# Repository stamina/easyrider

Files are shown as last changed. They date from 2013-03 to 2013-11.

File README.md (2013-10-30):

EasyRider
=========

EasyRider is a motorcycle telemetrics project, developed specifically for my Honda C90 classic bike.

The software is written in C for the Atmel AVR ATmega1284p main microcontroller.

The PCB was created with CadSoft Eagle 6.x, you'll find the schematic and board layout (including all components) in the /eagle directory.
The file /doc/info.txt also contains the [BOM] and some project notes. (Partly in Dutch)

_UPDATE:_ EasyRider REV B (github repo: easyriderb) is a completely new, smaller and more advanced board (mostly SMD parts) which also contains a GPS and WiFi module
for easy tracking and communicating with a mobile phone app.

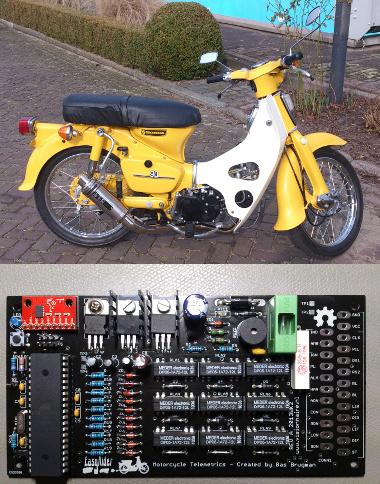
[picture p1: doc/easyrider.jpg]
Board and Bike


Functionality
-------------

EasyRider basically does the following things:

- Controls the lighting system: indicators, rear light, brake light, etc.
- Controls the claxon
- Contains a simple alarm system, based on an accelerometer
- Reads the motorcycle battery and gives a visual indication of the current voltage
- Contains a little buzzer for some funny startup sounds
- Contains a custom serial UART shell for communication with a terminal program or another microcontroller

Software
--------

The sofware is built around a simple *State Machine* pattern: when the driver is braking or toggling a switch, the software
is sending an event, which is handled by the correct event handler based on the current state (a bitmask of multiple substates).

The buzzer music was created with the **MIDICSV** MIDI to CSV conversion tool. The midi2byte.rb Ruby script converts the
plaintext CSV to a C header file containing an array of music notes.

The custom UART shell code is capable of registering commands and command handlers. E.g. typing "help" or "show state" in TeraTerm, Minicom, Putty
or any other serial terminal program. (configuration: 19200 baud/8N1)

*[BOM]: Bill Of Materials

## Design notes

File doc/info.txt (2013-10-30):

*info.txt* easyrider
" vim: filetype=help foldmethod=marker foldmarker=<<<,>>> modifiable noreadonly tw=0
" Author: Bas Brugman
" Website: www.visionnaire.nl

EasyRider REV A (Throughhole Edition) Telemetrics
-------------------------------------------------

Firmware 1.0 bug fixes:
----------------------

[X] BUG: Claxon mosfet switched aan bij veel toeren, voor zeer korte tijd -> oscillation?
      -> FIXED: Gemeten met scope: elke keer precies 15ms gate trigger, dus physical sense (drukknop claxon) maakt
         contact -> vergroten van 3x 5ms "debouncing" algoritme in code naar 6x
      -> duikt de 12V op gate naar beneden? waarom?
      -> Cap ervoor zetten?
      -> Grotere input cap bij 12V Regulator -> 1000uf, niet te hoge dimensie
      -> Transistor base resistor van 10K naar 2200 ohm?
      -> Cooler verwijderen: te veel capacitance?
      -> extra flyback diode (schottky) parallel aan mosfet? 
[X] BUG: The claxon sound continues when turning the alarm off by turning the ignition key on 
[X] TODO: Alarm mode: indicator blink slower -> every 4 timer1 ticks: 1 tick on 
[X] TODO: Alarm trigger time should be faster, 
[X] BUG: Ignition off: disable all lights/sounds
[X] BUG: Cockpit status light stays lit in alarm/alarmsettle mode ->  unwanted check_battery_read() calls
[X] BUG: Hardware related:  when claxon (2 amp) is pushed, all reed relays switch on: short blinks of lights
      -> snubber/flyback diode proberen
      -> Ground path van claxon terugvoeren via draad naar accu min-pole om groundloops te voorkomen
[X] BUG: Alarm trigger werkt niet lekker: claxon/blinkers sequence niet goed en transition from alarm_settle/alarm states foutief

REV A
-----

Firmware 1.1 features:
----------------------

- [ ] Bij debounce checks, is shifting << 5 wel nodig?
- [ ] Sound: Mountain King song erbij
- [ ] Change alarm claxon algorithme: count and resettle, ander algoritme -> 3de claxon sound kapt af, waarom?
- [ ] Extra timer gebruiken en flexibler/indepent maken van elkaar: losse blink timer
- [ ] Heartbeat LED uit na enige tijd
- [ ] Contact uit -> naar sleep mode -> meteen muziek uit 
- [ ] Contact uit -> alarm switch kan nog geactiveerd worden -> moet niet kunnen 
- [ ] Muziek mag nooit met indicatie beeps conflicteren 
- [ ] Splitsen hardware/software version strings -> beide in EEPROM
- [ ] "static"s nalopen
- [ ] backpedal code eruit halen
- [ ] in deep-sleep mode kan de mcu alleen via reset gestart worden -> FIXME

Firmware 1.0 features:
----------------------

- [X] Lighting System
- [X] Audio through Claxon and Buzzer
- [X] Battery status
- [X] Alarm, triggered by an accelerometer

- [X] PCB creation via Eagle CAD

- General functionality:
  [X] State Machine rules "exclusive"/"inclusive"
      [X] positive and negative substates parsing
      [X] sense reading moet uit te zetten zijn: enableSense/disableSense
      [X] event dispatching via psense reads, maar ook via dynamic senses (dyn_senses)
  [X] JTD uitzetten, zodat de poorten normaal gebruikt kunnen worden ->
       An IO control bit "JTD" is available. Unlike the fuses this bit can be
       set at run-time allowing you to disable the JTAG / OCD functionality in software
       during program execution.
  [X] Watchdog aanzetten, tegen vastlopers!
  [X] In production: OCD uitzetten ivm extra stroomverbruik

- Audio
  [X] Simple music via buzzer (Midi to CSV to .h binary conversion)

 [X] Claxon
  [X] Sound on Push button

 - Battery status
    [X] knipper status light cockpit:
      [X] normal operation -> continue branden
      [X] shutdown via switch -> uit
      [X] indien low battery -> slow knipper
      [X] indien high battery -> fast knipper

 - Alarm, triggered by an accelerometer
    [X] bij aanzetten -> 1x indicators aan voor x secs -> alarm settle time -> buzzer music
    [X] in active mode: cockpit indicator lamp knippert
    [X] Alarm triggered: alle lichten blinken, claxon repeat
    [X] Alarm triggered: na x secs -> reset -> accelerometer slaat nieuwe voltage waarden op

 - Light/Buzzer System
    [X] Indicators Left/Right
      [X] Buzzer mee laten piepen (software flag)
    [X] Rearlight
    [X] Brakelight
    [X] Pilotlight
    [X] Warning lights: 4x knipperbollen blinken en buzzer
    [X] Achteruitrij sensen met accelerometer -> "all indicators" en buzzer aan -> warning state

- Contact slot:
  Ignition uit: sense wire (SENSE_IGN) -> contact uit
    [X] naar ST_SLEEP mode
    [X] Na x secs naar mcu hardware sleep mode
      -> uitzetten van ADC, Watchdog en ports
      -> geen wakeup trigger, alleen een harde reset
  Ignition aan: sense wire (~SENSE_IGN) -> contact aan:
    [X] Alle lampen een paar seconden aan
    [X] startup sound / kleine muziekje
    [X] status wordt ST_NORMAL

- Shell Commands:
    [X] help -> show help menu / service menu
    [X] show
        [X] version
        [X] state (all substates / physical and dynamic senses)
        [X] volt (accu voltage / 3-axis voltages accelerometer)
        [X] conf (EEPROM struct, toon alle tSettings tegelijk):
    [X] set 
        [X] dynamic senses
        [X] conf (settings in EEPROM struct)
    [X] reset (software reset mcu via watchdog)

Statistics
----------

(2.9Ah Gel battery)

Power EasyRider Board REV A:
  Normal mode:     54mA
  Sleep mode:      44mA (pcb led brandt nog!)
  Alarm mode:      80mA (indicator relay on/off)
  Deep Sleep mode: 10mA (mcu Power Down) -> accu leeg na 12 dagen

BOM "EasyRider" REV A
---------------------

[X] 1x Atmel ATMEGA1284p 40 pins DIP
[X] 9x Meder Reed relays DIP05-1A72-12L 
[X] 10x 1N4007 diode
[X] 1x 1N5400 diode
[X] 11x 5.6V zener diode (10 senses, 1 voltage divider)
[X] 1x 100k resistor 1% 
[X] 1x 18k resistor 1% 
[X] 4x 10k resistor 5%  (pullups reset mcu and slp accelerometer en trans./mosfet gate)
[X] 11x 220 resistor 5% (10 senses, 1 heartbeat LED)
[X] 1x 330 resistor (reset btn current limiter)
[X] 1x 10 ohm 5 watt resistor
[X] 1x 6 amp fuse holder voor 5x20
[X] 1x 1A PTC 3,2 x 1,5 mm, hoog 1,05 mm -> van littelfuse "M" marking 15V!
[X] 1x 25V Varistor JVR05N390K (5mm pitch)
[X] 1x 470uf cap electrolytic for filtering 
[X] 1x 47uf low ESR cap electrolytic for filtering 
[X] 1x 10uf output filter cap for LF33CV
[X] 2x 100nf cap electrolytic for filtering
[X] 3x 100nf cap ceramic for bypassing
[X] 2x 22pf cap ceramic for crystal
[X] 1x 20mhz crystal
[X] 1x LM2940 regulator (TO-220)
[X] 1x LF33CV regulator (TO-220)
[X] 1x P-Channel MOSFET IRF4905PBF 
[X] 1x NPN 2N3904 transistor
[X] 1x reset button 4 pins 
[X] 1x buzzer (4.1khz 83db met sticker bovenop PK12N40PETQ)
[X] 1x 3mm blue status led 
[X] 1x shrouded ISP 6 pin (2x3) header (zie dangerousprototypes.com lib)
[X] 1x 2 pin header UART 
[X] 1x MMA7361 Freescale Accelerometer breakout pins 
[X] 1x 24 pin main wire connector

Extra: (external or added later on)
[X] 1x flyback diode parallel across claxon: SB540E SCHOTTKY 40V 5A
[X] 1x 1000uf cap electrolytic for filtering 

Schematic/Board
---------------

[X] ULP runnen voor re-ordering designators
[X] +/- 10 via's plaatsen voor koppelen GND planes 
[X] 4x drill hole 4mm (3mm x/y spacing zijkanten board)
[X] 2x drill hole 3mm voor accelerometer board stabiliteitspunten
[X] 4x Test Point TP (12v, 5V, 3.3v, GND) uit standard "testpad" library
[X] Import BMP logo met import-bmp.ulp, settings: Scaled, Mil, 0.3 Scale, Layer 21

Eagle settings:
--------------

- 1 oz copper thickness (35µm)
- diameter drills voor bevestiging +/- 3.5mm
- diameter voor via's = +/- 27 mil, voor 20 mil traces: 32 mil via's, let op dat outer-diameter niet te smal wordt:
    aanpassen restring -> iets groter zetten
- trace thickness:
    10 mil (1 amp) standaard SMD signal tracks
    16 mil (15-20 mil) for through-hole pads
    20 mil 3.3v/5v/12v seperate tracks/gnd tracks (3 amp)
    70 mil (6 amp) incoming 12v/GND track
- spacing between traces: minimum 10 mil 
- Isolation between GND polygons and other components/tracks: 15 mil
- Oval TH: 0.0314 inch (0.8 mm) diameter holes -> pad widths: 1.3-1.5 mm
- Oval TH: for 1mm2 draad (EasyRider connector): diameter holes: 1.9mm -> 0.074 inch
- Round TH: voor 1A diodes etc: 0.040 inch (1.1 mm) diameter holes
- Round TH: voor dikke 3A diodes etc: 0.059 inch (1.498 mm) diameter holes
- Round TH: voor standard diodes/resistors: 0.032 inch (0.81 mm) diameter holes
- Length/pitch for standard diodes/resistors: 0.4 inch (10.16 mm) of 0.5 inch (12.7 mm)
- Length/pitch for dikke high watt resistors: 1.15 inch (29.21 mm)
- text: always as vectors: 50 mil/0.05 inch size, 16% ratio == 8mil width, line distance 50%: (size*ratio/100 == width of text lines) 

Eagle layers:

- tNames: voor >NAME teksten
- tValues: voor >VALUE teksten
- tPlace: silkscreen lijnen/tekst/outlines -> (8 mil/0.008 inch width, gebruik een 0.025 inch afstandsgrid van pads/tracks: no overlapping!)
- tDocu: outlines van alle packages (alleen ter controle voor spacing en printouts: past het allemaal naast elkaar) -> geef een gele kleur (5 mil width)

EuroCircuits.com export settings:
---------------------------------

Gewoon de .brd uploaden, of:

CAM processor: gerb274x.cam

4 layers selecteren: Component side (.CMP)       = 1 Top layer / 17 Pads layer / 18 Vias layer / 20 Dimension layer
4 layers selecteren: Solder side (.SOL)          = 16 Bot layer / 17 Pads layer / 18 Vias layer / 20 Dimension layer
3 layers selecteren: Silk screen CMP (.PLC) 	   = 20 Dimension layer / 21 tPlace layer / 25 tNames layer
2 layers selecteren: Solder stop mask CMP (.STC) = 20 Dimension layer / 29 tStop layer
2 layers selecteren: Solder stop mask SOL (.STS) = 20 Dimension layer / 30 bStop layer

CAM processor: excellon.cam

2 layers selecteren: Excellon drill (.DRD)       = 44 Drills layer / 45 Holes layer

NOTE: Cream (solderpaste) en milling/measures layers niet nodig.
      Let op dat alle .extensies uniek zijn!

You then click process job and the Excellon file will be generated.
You now simply combine all these files into a single zip file and upload it via the Eurocircuits website.

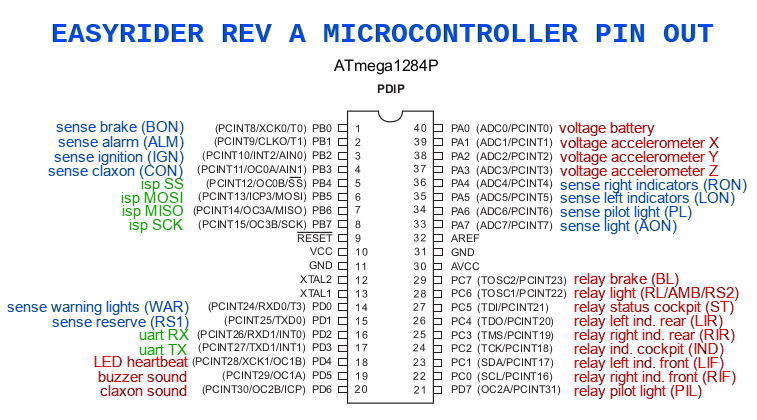
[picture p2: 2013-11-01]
doc/easyrider_reva_mcu_pinout.png

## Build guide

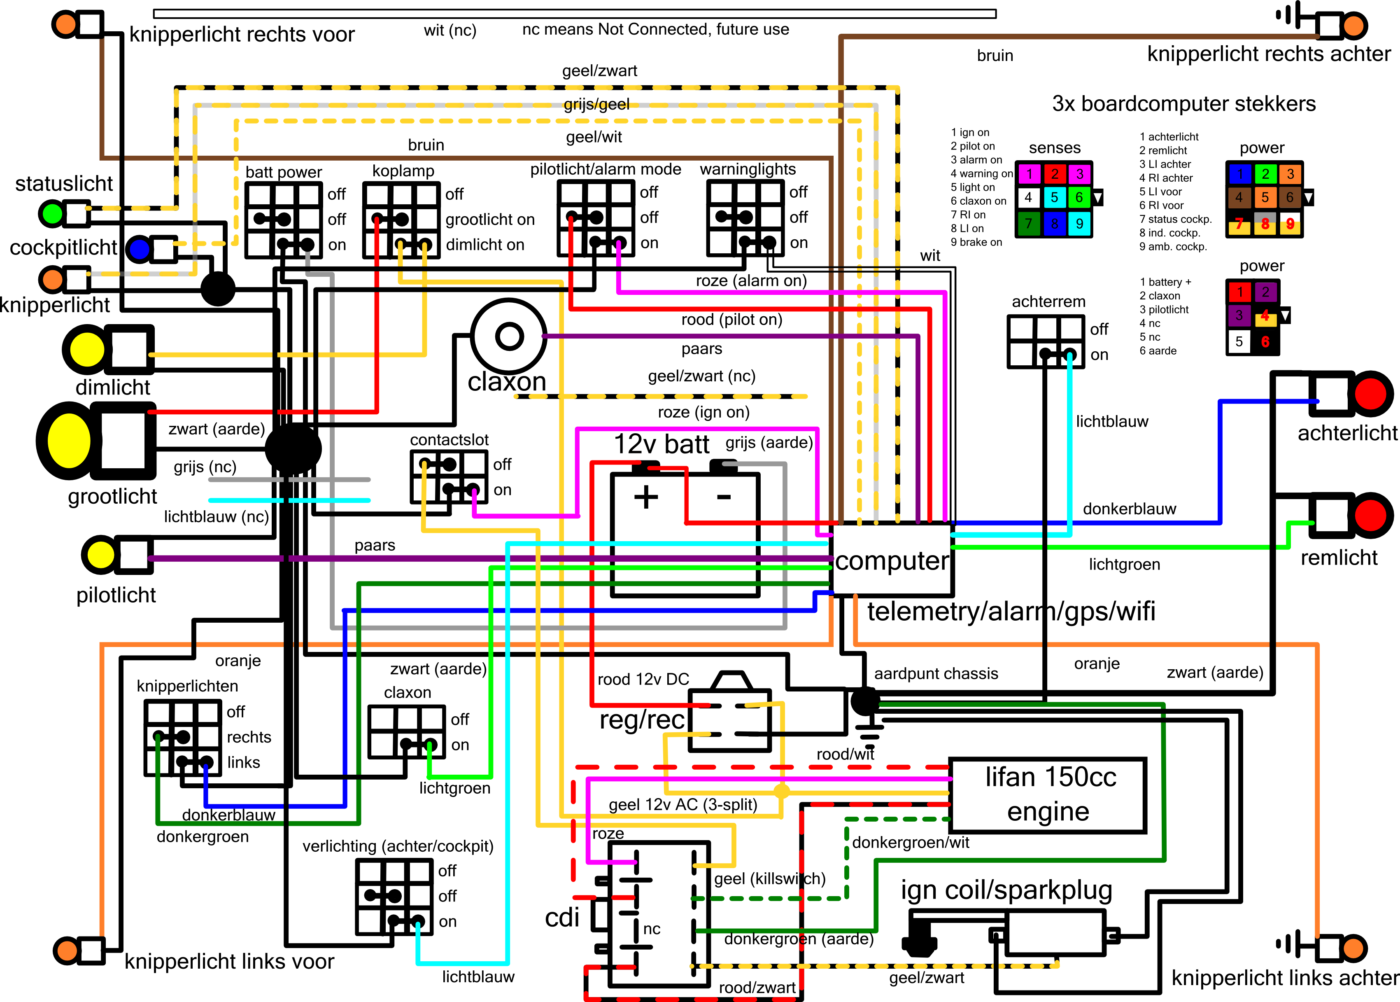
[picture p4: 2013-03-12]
doc/hondac90_lifan150_wiring.png

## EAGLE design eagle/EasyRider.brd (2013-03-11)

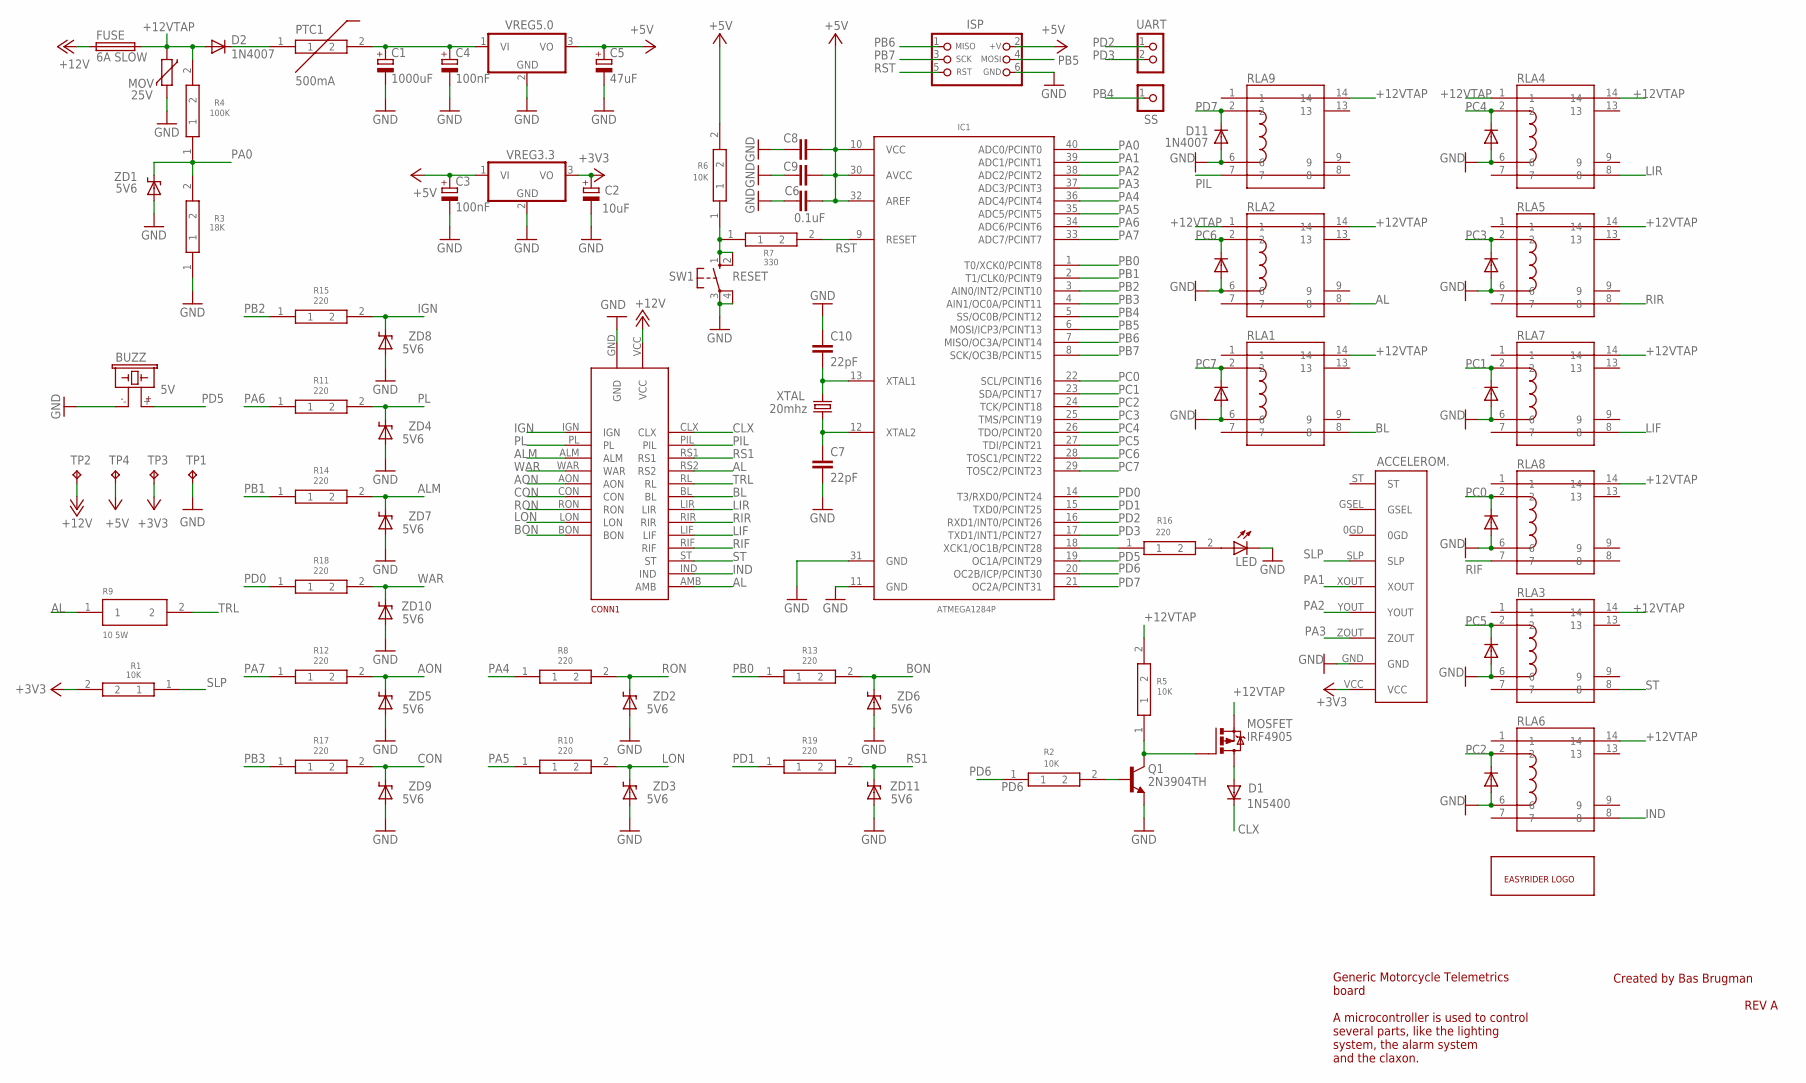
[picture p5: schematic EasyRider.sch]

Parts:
ACCELEROM.: MMA7361FREESCALE; BREAKOUT
BUZZ: 5V; 0.3PITCH
C1: 1000uF; E5-10,5
C2: 10uF; E2,5-4R
C3, C4: 100nF; E2,5-4R
C5: 47uF; E2,5-7
C6, C8, C9: 0.1uF; C025-024X044
C7, C10: 22pF; C025-024X044
CONN1: EASYRIDER_CONNDIP; SIL
D1: 1N5400; DO201-15
D2, D11: 1N4007; DIP_1N4007
D3, D4, D5, D6, D7, D8, D9, D10: 1N4007DIP; DIP_1N4007
FUSE: 6A SLOW; SH22,5A
IC1: ATMEGA1284P; DIL40
ISP: CON_HEADER_PRG_AVR_ICSP-PTH; HEADER_PRG_2X03
LED: LEDDIP; LED3MM
MOSFET: IRF4905; TO220
MOV: 25V; R-5
PTC1: 500mA; PTC
Q1: 2N3904TH; TO92
R1, R2, R5, R6: 10K; RESISTOR
R3: 18K; RESISTOR
R4: 100K; RESISTOR
R7: 330; RESISTOR
R8, R10, R11, R12, R13, R14, R15, R16, R17, R18, R19: 220; RESISTOR
R9: 10 5W; RESISTOR
RLA1, RLA2, RLA3, RLA4, RLA5, RLA6, RLA7, RLA8, RLA9: MEDER_REED_DIP05-1A72-12LDIP; DIP05-1A72-12L
SS: CON_HEADER_1X01-PTH; M1X1
SW1: RESET; DIP45MM_56MM_PITCH
TP1, TP2, TP3, TP4: TPTP20SQ; TP20SQ
U$1: EASYRIDER_LOGO
UART: CON_HEADER_1X02-PTH; M1X2
VREG3.3, VREG5.0: VREG_IGODIP; TO220
XTAL: 20mhz; HC49/S
ZD1, ZD2, ZD3, ZD4, ZD5, ZD6, ZD7, ZD8, ZD9, ZD10, ZD11: 5V6; DIODE_ZENER_56

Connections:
+3V3: ACCELEROM..VCC, C2.+, R1.2, TP3.TP, VREG3.3.3 (VO)
+5V: C3.+, C5.+, C6.2, C8.2, C9.2, IC1.10 (VCC), IC1.30 (AVCC), IC1.32 (AREF), ISP.2 (+V), R6.2, TP4.TP, VREG3.3.1 (VI), VREG5.0.3 (VO)
+12V: CONN1.VCC, FUSE.1, TP2.TP
+12VTAP: D2.A, FUSE.2, MOSFET.S, MOV.1, R4.2, R5.2, RLA1.14, RLA2.1, RLA2.14, RLA3.14, RLA4.1, RLA4.14, RLA5.14, RLA6.14, RLA7.14, RLA8.14, RLA9.14
AL: CONN1.AMB, CONN1.RS2, R9.1, RLA2.8
ALM: CONN1.ALM, R14.2, ZD7.C
AON: CONN1.AON, R12.2, ZD5.C
BL: CONN1.BL, RLA1.8
BON: CONN1.BON, R13.2, ZD6.C
CLX: CONN1.CLX, D1.C
CON: CONN1.CON, R17.2, ZD9.C
GND: ACCELEROM..GND, BUZZ.- (1), C1.-, C2.-, C3.-, C4.-, C5.-, C6.1, C7.2, C8.1, C9.1, C10.1, CONN1.GND, D3.A, D4.A, D5.A, D6.A, D7.A, D8.A, D9.A, D10.A, D11.A, IC1.11 (GND), IC1.31 (GND), ISP.6 (GND), LED.K (C), MOV.2, Q1.3 (E), R3.1, RLA1.6, RLA2.6, RLA3.6, RLA4.6, RLA5.6, RLA6.6, RLA7.6, RLA8.6, RLA9.6, SW1.3, SW1.4, TP1.TP, VREG3.3.2 (GND), VREG5.0.2 (GND), ZD1.A, ZD2.A, ZD3.A, ZD4.A, ZD5.A, ZD6.A, ZD7.A, ZD8.A, ZD9.A, ZD10.A, ZD11.A
IGN: CONN1.IGN, R15.2, ZD8.C
IND: CONN1.IND, RLA6.8
LIF: CONN1.LIF, RLA7.8
LIR: CONN1.LIR, RLA4.8
LON: CONN1.LON, R10.2, ZD3.C
unnamed: C7.1, IC1.12 (XTAL2), XTAL.1
unnamed: C10.2, IC1.13 (XTAL1), XTAL.2
unnamed: R6.1, R7.1, SW1.1, SW1.2
unnamed: IC1.18 (XCK1/OC1B/PCINT28), R16.1
unnamed: MOSFET.G, Q1.1 (C), R5.1
unnamed: D1.A, MOSFET.D
unnamed: LED.A, R16.2
unnamed: C1.+, C4.+, PTC1.2, VREG5.0.1 (VI)
unnamed: D2.C, PTC1.1
unnamed: Q1.2 (B), R2.2
PA0: IC1.40 (ADC0/PCINT0), R3.2, R4.1, ZD1.C
PA1: ACCELEROM..XOUT, IC1.39 (ADC1/PCINT1)
PA2: ACCELEROM..YOUT, IC1.38 (ADC2/PCINT2)
PA3: ACCELEROM..ZOUT, IC1.37 (ADC3/PCINT3)
PA4: IC1.36 (ADC4/PCINT4), R8.1
PA5: IC1.35 (ADC5/PCINT5), R10.1
PA6: IC1.34 (ADC6/PCINT6), R11.1
PA7: IC1.33 (ADC7/PCINT7), R12.1
PB0: IC1.1 (T0/XCK0/PCINT8), R13.1
PB1: IC1.2 (T1/CLK0/PCINT9), R14.1
PB2: IC1.3 (AIN0/INT2/PCINT10), R15.1
PB3: IC1.4 (AIN1/OC0A/PCINT11), R17.1
PB4: IC1.5 (SS/OC0B/PCINT12), SS.1
PB5: IC1.6 (MOSI/ICP3/PCINT13), ISP.4 (MOSI)
PB6: IC1.7 (MISO/OC3A/PCINT14), ISP.1 (MISO)
PB7: IC1.8 (SCK/OC3B/PCINT15), ISP.3 (SCK)
PC0: D10.C, IC1.22 (SCL/PCINT16), RLA8.2
PC1: D9.C, IC1.23 (SDA/PCINT17), RLA7.2
PC2: D8.C, IC1.24 (TCK/PCINT18), RLA6.2
PC3: D7.C, IC1.25 (TMS/PCINT19), RLA5.2
PC4: D6.C, IC1.26 (TDO/PCINT20), RLA4.2
PC5: D5.C, IC1.27 (TDI/PCINT21), RLA3.2
PC6: D4.C, IC1.28 (TOSC1/PCINT22), RLA2.2
PC7: D3.C, IC1.29 (TOSC2/PCINT23), RLA1.2
PD0: IC1.14 (T3/RXD0/PCINT24), R18.1
PD1: IC1.15 (TXD0/PCINT25), R19.1
PD2: IC1.16 (RXD1/INT0/PCINT26), UART.1
PD3: IC1.17 (TXD1/INT1/PCINT27), UART.2
PD5: BUZZ.+ (2), IC1.19 (OC1A/PCINT29)
PD6: IC1.20 (OC2B/ICP/PCINT30), R2.1
PD7: D11.C, IC1.21 (OC2A/PCINT31), RLA9.2
PIL: CONN1.PIL, RLA9.7
PL: CONN1.PL, R11.2, ZD4.C
RIF: CONN1.RIF, RLA8.7
RIR: CONN1.RIR, RLA5.8
RON: CONN1.RON, R8.2, ZD2.C
RS1: CONN1.RS1, R19.2, ZD11.C
RST: IC1.9 (RESET), ISP.5 (RST), R7.2
SLP: ACCELEROM..SLP, R1.1
ST: CONN1.ST, RLA3.8
TRL: CONN1.RL, R9.2
WAR: CONN1.WAR, R18.2, ZD10.C

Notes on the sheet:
Created by Bas Brugman
REV A
Generic Motorcycle Telemetrics board A microcontroller is used to control several parts, like the lighting system, the alarm system and the claxon.

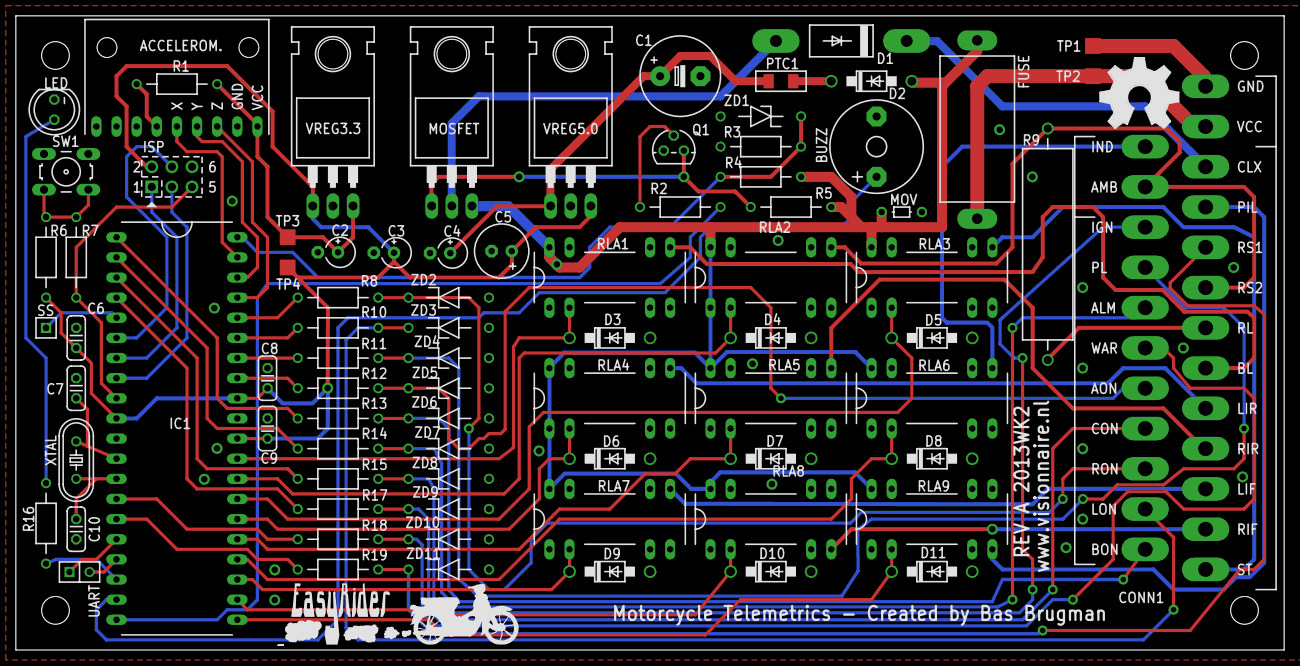
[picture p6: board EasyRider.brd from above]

Board: 2 copper layers, 160.0 x 80.0 mm, 83 parts (0 on the bottom side), 69 nets.

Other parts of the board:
U$2: OSHW_FILLX350_NOTEXT

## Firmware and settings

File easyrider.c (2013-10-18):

/*
 *
 *  Copyright (C) 2013 Bas Brugman
 *  http://www.visionnaire.nl
 *
 *  Licensed under the Apache License, Version 2.0 (the "License");
 *  you may not use this file except in compliance with the License.
 *  You may obtain a copy of the License at
 *
 *    http://www.apache.org/licenses/LICENSE-2.0
 *
 *  Unless required by applicable law or agreed to in writing, software
 *  distributed under the License is distributed on an "AS IS" BASIS,
 *  WITHOUT WARRANTIES OR CONDITIONS OF ANY KIND, either express or implied.
 *  See the License for the specific language governing permissions and
 *  limitations under the License.
 *
 */
#include <avr/io.h>
#include <avr/interrupt.h>
#include <avr/pgmspace.h>
#include <avr/eeprom.h>
#include <avr/wdt.h>
#include <avr/sleep.h>
#include <avr/power.h>
#include <stdlib.h>
#include <stdint.h>
#include <string.h>

#include "command.h"
#include "usart.h"
#include "command_usart.h"
#include "command_handlers.h"
#include "easyrider.h"

#include "sound/alarm.h"
#include "sound/frogger.h"
#include "sound/furelise.h"
#include "sound/larry.h"
#include "sound/pipi.h"
#include "sound/popcorn.h"

// state transition struct array: handler assigment for state/event combo's
tTransition g_trans[] = {
  {check_claxon_on, EV_CLAXON_ON, process_claxon_on},
  {check_claxon_off, EV_CLAXON_OFF, process_claxon_off},
  {check_ri_on, EV_RI_ON, process_ri_on},
  {check_ri_off, EV_RI_OFF, process_ri_off},
  {check_li_on, EV_LI_ON, process_li_on},
  {check_li_off, EV_LI_OFF, process_li_off},
  {check_ign_on, EV_IGN_ON, process_ign_on},
  {check_ign_off, EV_IGN_OFF, process_ign_off},
  {check_alarm_on, EV_ALARM_ON, process_alarm_on},
  {check_alarm_off, EV_ALARM_OFF, process_alarm_off},
  {check_brake_on, EV_BRAKE_ON, process_brake_on},
  {check_brake_off, EV_BRAKE_OFF, process_brake_off},
  {check_pilot_on, EV_PILOT_ON, process_pilot_on},
  {check_pilot_off, EV_PILOT_OFF, process_pilot_off},
  {check_light_on, EV_LIGHT_ON, process_light_on},
  {check_light_off, EV_LIGHT_OFF, process_light_off},
  {check_battery_read, EV_READ_BATT, process_battery},
  {check_warning_on, EV_WARNING_ON, process_warning_on},
  {check_warning_off, EV_WARNING_OFF, process_warning_off},
  {check_backpedal_on, EV_BACKPEDAL, process_backpedal}
};

static uint16_t get_substate(uint16_t st) {
  return (g_state & st);
}

static void set_substate(uint16_t st) {
  g_state |= st;
}

static void remove_substate(uint16_t st) {
  g_state &= ~st;
}

// Gets called from the main loop, reads all senses and puts them in the event queue.
// The complete queue is handled (emptied) in each main loop iteration in a FIFO way, so better
// put the higher priority events at the top, i.e. claxon sound is more important then indicator light.
static void dispatch_events() {
  check_brake();
  check_claxon();
  check_ri();
  check_li();
  check_light();
  check_pilot();
  check_ign();
  check_settle();
  check_sound();
  check_alarm();
  check_alarm_settle();
  check_alarm_trigger();
  check_battery();
  check_warning();
  check_sleep();
  if (g_settings.backpedal) {
    check_backpedal();
  }
}

uint8_t check_battery_read() {
  return ((g_state & ~(ST_ALARM | ST_ALARM_SETTLE | ST_SETTLE | ST_SLEEP)) == g_state);
}

uint8_t check_ri_on() {
  return (((g_state & (ST_NORMAL | ST_RI | ST_CLAXON | ST_BRAKE | ST_LIGHT | ST_PILOT)) == g_state) &&
        ((g_state & ~(ST_LI | ST_ALARM | ST_ALARM_SETTLE | ST_SETTLE | ST_WARNING | ST_SLEEP)) == g_state));
}

uint8_t check_li_on() {
  return (((g_state & (ST_NORMAL | ST_LI | ST_CLAXON | ST_BRAKE | ST_LIGHT | ST_PILOT)) == g_state) &&
        ((g_state & ~(ST_RI | ST_ALARM | ST_ALARM_SETTLE | ST_SETTLE | ST_WARNING | ST_SLEEP)) == g_state));
}

uint8_t check_brake_on() {
  return (((g_state & (ST_NORMAL | ST_RI | ST_LI | ST_CLAXON | ST_LIGHT | ST_PILOT | ST_WARNING)) == g_state) &&
        ((g_state & ~(ST_BRAKE | ST_ALARM | ST_ALARM_SETTLE | ST_SETTLE | ST_SLEEP)) == g_state));
}

uint8_t check_warning_on() {
  // warning blinks override RI/LI
  return (((g_state & (ST_NORMAL | ST_WARNING | ST_RI | ST_LI | ST_CLAXON | ST_LIGHT | ST_PILOT | ST_BRAKE )) == g_state) &&
        ((g_state & ~(ST_ALARM | ST_ALARM_SETTLE | ST_SETTLE | ST_SLEEP)) == g_state));
}

uint8_t check_pilot_on() {
  return (((g_state & (ST_NORMAL | ST_RI | ST_LI | ST_CLAXON | ST_LIGHT | ST_BRAKE | ST_WARNING)) == g_state) &&
        ((g_state & ~(ST_PILOT | ST_ALARM | ST_ALARM_SETTLE | ST_SETTLE | ST_SLEEP)) == g_state));
}

uint8_t check_light_on() {
  return (((g_state & (ST_NORMAL | ST_RI | ST_LI | ST_CLAXON | ST_PILOT | ST_BRAKE | ST_WARNING)) == g_state) &&
        ((g_state & ~(ST_LIGHT | ST_ALARM | ST_ALARM_SETTLE | ST_SETTLE | ST_SLEEP)) == g_state));
}

uint8_t check_backpedal_on() {
  return (((g_state & (ST_NORMAL | ST_LIGHT | ST_CLAXON | ST_PILOT | ST_BRAKE )) == g_state) &&
        ((g_state & ~(ST_WARNING | ST_RI | ST_LI | ST_ALARM | ST_ALARM_SETTLE | ST_SETTLE | ST_SLEEP)) == g_state));
}

uint8_t check_claxon_on() {
  return (((g_state & (ST_NORMAL | ST_RI | ST_LI | ST_BRAKE | ST_LIGHT | ST_PILOT | ST_WARNING)) == g_state) &&
        ((g_state & ~(ST_CLAXON | ST_ALARM | ST_ALARM_SETTLE | ST_SETTLE | ST_SLEEP)) == g_state));
}

uint8_t check_ign_on() {
  return ((g_state & (ST_SLEEP | ST_ALARM_SETTLE | ST_ALARM)) == g_state);
}

uint8_t check_alarm_on() {
  //BUG: change this..
  return ((g_state & ST_SLEEP) == g_state);
}

uint8_t check_ri_off() {
 return ((ST_RI & g_state) == ST_RI);
}

uint8_t check_li_off() {
 return ((ST_LI & g_state) == ST_LI);
}

uint8_t check_claxon_off() {
 return ((ST_CLAXON & g_state) == ST_CLAXON);
}

uint8_t check_pilot_off() {
 return ((ST_PILOT & g_state) == ST_PILOT);
}

uint8_t check_brake_off() {
 return ((ST_BRAKE & g_state) == ST_BRAKE);
}

uint8_t check_warning_off() {
 return ((ST_WARNING & g_state) == ST_WARNING);
}

uint8_t check_light_off() {
 return ((ST_LIGHT & g_state) == ST_LIGHT);
}

uint8_t check_ign_off() {
  return ((g_state & ~(ST_SLEEP | ST_ALARM | ST_ALARM_SETTLE)) == g_state);
}

uint8_t check_alarm_off() {
  // alarm can't be switched off in alarm state, only explicitly in alarm_settle mode
  // or automatically when ignition is switched on
  return ((g_state & (ST_ALARM_SETTLE)) == g_state);
}

void check_ri() {
  // pin senses
  if ((g_senses & FLAG_SENSE_LIGHT_RI) == FLAG_SENSE_LIGHT_RI) {
    if (~STATUS_C90_SENSE_LIGHT_RI) { // low, RI on
      set_event(EV_RI_ON);
    }
    if (STATUS_C90_SENSE_LIGHT_RI) { // RI off
      set_event(EV_RI_OFF);
    }
  }
  // dynamic senses
  if ((g_dyn_senses & FLAG_SENSE_LIGHT_RI) == FLAG_SENSE_LIGHT_RI) {
    if ((g_dyn_senses_status & FLAG_SENSE_LIGHT_RI) == FLAG_SENSE_LIGHT_RI) { // high, RI off
      set_event(EV_RI_OFF);
    } else {
      set_event(EV_RI_ON); // RI on
    }
  }
}

void check_li() {
  // pin senses
  if ((g_senses & FLAG_SENSE_LIGHT_LI) == FLAG_SENSE_LIGHT_LI) {
    if (~STATUS_C90_SENSE_LIGHT_LI) { // low, LI on
      set_event(EV_LI_ON);
    }
    if (STATUS_C90_SENSE_LIGHT_LI) { // LI off
      set_event(EV_LI_OFF);
    }
  }
  // dynamic senses
  if ((g_dyn_senses & FLAG_SENSE_LIGHT_LI) == FLAG_SENSE_LIGHT_LI) {
    if ((g_dyn_senses_status & FLAG_SENSE_LIGHT_LI) == FLAG_SENSE_LIGHT_LI) { // high, LI off
      set_event(EV_LI_OFF);
    } else {
      set_event(EV_LI_ON); // LI on
    }
  }
}

void check_claxon() {
  // pin senses
  if ((g_senses & FLAG_SENSE_CLAXON) == FLAG_SENSE_CLAXON) {
    if (~STATUS_C90_SENSE_CLAXON) {
      set_event(EV_CLAXON_ON);
    }
    if (STATUS_C90_SENSE_CLAXON) {
      set_event(EV_CLAXON_OFF);
    }
  }
  // dynamic senses
  if ((g_dyn_senses & FLAG_SENSE_CLAXON) == FLAG_SENSE_CLAXON) {
    if ((g_dyn_senses_status & FLAG_SENSE_CLAXON) == FLAG_SENSE_CLAXON) {
      set_event(EV_CLAXON_OFF);
    } else {
      set_event(EV_CLAXON_ON);
    }
  }
}

void check_pilot() {
  // pin senses
  if ((g_senses & FLAG_SENSE_PILOT) == FLAG_SENSE_PILOT) {
    if (~STATUS_C90_SENSE_PILOT) {
      set_event(EV_PILOT_ON);
    }
    if (STATUS_C90_SENSE_PILOT) {
      set_event(EV_PILOT_OFF);
    }
  }
  // dynamic senses
  if ((g_dyn_senses & FLAG_SENSE_PILOT) == FLAG_SENSE_PILOT) {
    if ((g_dyn_senses_status & FLAG_SENSE_PILOT) == FLAG_SENSE_PILOT) {
      set_event(EV_PILOT_OFF);
    } else {
      set_event(EV_PILOT_ON);
    }
  }
}

void check_light() {
  // pin senses
  if ((g_senses & FLAG_SENSE_LIGHT) == FLAG_SENSE_LIGHT) {
    if (~STATUS_C90_SENSE_LIGHT) {
      set_event(EV_LIGHT_ON);
    }
    if (STATUS_C90_SENSE_LIGHT) {
      set_event(EV_LIGHT_OFF);
    }
  }
  // dynamic senses
  if ((g_dyn_senses & FLAG_SENSE_LIGHT) == FLAG_SENSE_LIGHT) {
    if ((g_dyn_senses_status & FLAG_SENSE_LIGHT) == FLAG_SENSE_LIGHT) {
      set_event(EV_LIGHT_OFF);
    } else {
      set_event(EV_LIGHT_ON);
    }
  }
}

void check_brake() {
  // pin senses
  if ((g_senses & FLAG_SENSE_BRAKE) == FLAG_SENSE_BRAKE) {
    if (~STATUS_C90_SENSE_BRAKE) {
      set_event(EV_BRAKE_ON);
    }
    if (STATUS_C90_SENSE_BRAKE) {
      set_event(EV_BRAKE_OFF);
    }
  }
  // dynamic senses
  if ((g_dyn_senses & FLAG_SENSE_BRAKE) == FLAG_SENSE_BRAKE) {
    if ((g_dyn_senses_status & FLAG_SENSE_BRAKE) == FLAG_SENSE_BRAKE) {
      set_event(EV_BRAKE_OFF);
    } else {
      set_event(EV_BRAKE_ON);
    }
  }
}

void check_ign() {
  // pin senses
  if ((g_senses & FLAG_SENSE_IGN) == FLAG_SENSE_IGN) {
    if (~STATUS_C90_SENSE_IGN) {
      set_event(EV_IGN_ON);
    }
    if (STATUS_C90_SENSE_IGN) {
      set_event(EV_IGN_OFF);
    }
  }
  // dynamic senses
  if ((g_dyn_senses & FLAG_SENSE_IGN) == FLAG_SENSE_IGN) {
    if ((g_dyn_senses_status & FLAG_SENSE_IGN) == FLAG_SENSE_IGN) {
      set_event(EV_IGN_OFF);
    } else {
      set_event(EV_IGN_ON);
    }
  }
}

void check_alarm() {
  // pin senses
  if ((g_senses & FLAG_SENSE_ALARM) == FLAG_SENSE_ALARM) {
    if (~STATUS_C90_SENSE_ALARM) {
      set_event(EV_ALARM_ON);
    }
    if (STATUS_C90_SENSE_ALARM) {
      set_event(EV_ALARM_OFF);
    }
  }
  // dynamic senses
  if ((g_dyn_senses & FLAG_SENSE_ALARM) == FLAG_SENSE_ALARM) {
    if ((g_dyn_senses_status & FLAG_SENSE_ALARM) == FLAG_SENSE_ALARM) {
      set_event(EV_ALARM_OFF);
    } else {
      set_event(EV_ALARM_ON);
    }
  }
}

void check_battery() {
  if (check_battery_read()) {
    set_event(EV_READ_BATT);
  }
}

void check_sleep() {
  if (g_state == ST_SLEEP) {
    if (g_sleep_counter == 0) {
      sleep_now();
    }
  } else {
    // TODO: why set this repeatable?
    g_sleep_counter = g_settings.deep_sleep_counter;
  }
}

void check_backpedal() {
  if (check_backpedal_on()) {
    set_event(EV_BACKPEDAL);
  }
}

void check_warning() {
  // pin senses
  if ((g_senses & FLAG_SENSE_WARNING) == FLAG_SENSE_WARNING) {
    if (~STATUS_C90_SENSE_WARNING) {
      set_event(EV_WARNING_ON);
    }
    if (STATUS_C90_SENSE_WARNING) {
      set_event(EV_WARNING_OFF);
    }
  }
  // dynamic senses
  if ((g_dyn_senses & FLAG_SENSE_WARNING) == FLAG_SENSE_WARNING) {
    if ((g_dyn_senses_status & FLAG_SENSE_WARNING) == FLAG_SENSE_WARNING) {
      set_event(EV_WARNING_OFF);
    } else {
      set_event(EV_WARNING_ON);
    }
  }
}

void check_settle() {
  if (g_state == ST_SETTLE) {
    if (!FLAG_SETTLE) { // first time in settle mode
      uint8_t song_idx = g_settings.startup_sound;
      FLAG_SETTLE = 1;
      // activate all lights
      PORT_C90_LIGHT_INDICATOR_COCKPIT |= (1 << PIN_C90_LIGHT_INDICATOR_COCKPIT);
      PORT_C90_LIGHT_STATUS_COCKPIT |= (1 << PIN_C90_LIGHT_STATUS_COCKPIT);
      PORT_C90_LIGHT_RI_F |= (1 << PIN_C90_LIGHT_RI_F);
      PORT_C90_LIGHT_RI_B |= (1 << PIN_C90_LIGHT_RI_B);
      PORT_C90_LIGHT_LI_F |= (1 << PIN_C90_LIGHT_LI_F);
      PORT_C90_LIGHT_LI_B |= (1 << PIN_C90_LIGHT_LI_B);
      PORT_C90_BRAKE |= (1 << PIN_C90_BRAKE);
      PORT_C90_PILOT |= (1 << PIN_C90_PILOT);
      PORT_C90_LIGHT |= (1 << PIN_C90_LIGHT);
      PORT_C90_CLAXON &= ~(1 << PIN_C90_CLAXON); // silence a possible claxon from the alarm
      // check voltage and activate according sound
      g_music_duration = 0;
      // check for random startup song
      if (song_idx == 0) {
        srand(g_adc_voltage[0] + g_adc_voltage[1] + g_adc_voltage[2] + g_adc_voltage[3]); // kinda random seed
        song_idx = 2 + (uint8_t)(rand() / (RAND_MAX / 5));
      }
      g_current_music = (uint16_t*)pgm_read_word(&g_music[song_idx-1]);
      g_selected_music = (uint16_t*)pgm_read_word(&g_music[song_idx-1]);
      FLAG_MUSIC = 1;
      g_current_settle_time = g_settings.settle_time;
    }
    if (!g_current_settle_time) { // settle time is over
      FLAG_SETTLE = 0; // reset settle
      g_state = ST_NORMAL;
      PORT_C90_LIGHT_INDICATOR_COCKPIT &= ~(1 << PIN_C90_LIGHT_INDICATOR_COCKPIT);
      PORT_C90_LIGHT_STATUS_COCKPIT &= ~(1 << PIN_C90_LIGHT_STATUS_COCKPIT);
      PORT_C90_LIGHT_RI_F &= ~(1 << PIN_C90_LIGHT_RI_F);
      PORT_C90_LIGHT_RI_B &= ~(1 << PIN_C90_LIGHT_RI_B);
      PORT_C90_LIGHT_LI_F &= ~(1 << PIN_C90_LIGHT_LI_F);
      PORT_C90_LIGHT_LI_B &= ~(1 << PIN_C90_LIGHT_LI_B);
      PORT_C90_CLAXON &= ~(1 << PIN_C90_CLAXON);
      PORT_C90_BRAKE &= ~(1 << PIN_C90_BRAKE);
      PORT_C90_PILOT &= ~(1 << PIN_C90_PILOT);
      PORT_C90_LIGHT &= ~(1 << PIN_C90_LIGHT);
    }
  }
}

void check_alarm_settle() {
  if (g_state == ST_ALARM_SETTLE) {
    if (!FLAG_ALARM_SETTLE) { // first time in alarm settle mode
      uint8_t song_idx = g_settings.alarm_sound;
      // check for random startup song
      if (song_idx == 0) {
        srand(g_adc_voltage[0] + g_adc_voltage[1] + g_adc_voltage[2] + g_adc_voltage[3]); // kinda random seed
        song_idx = 1 + (uint8_t)(rand() / (RAND_MAX / 6));
      }
      FLAG_ALARM_SETTLE = 1;
      // activate indicators
      PORT_C90_LIGHT_INDICATOR_COCKPIT |= (1 << PIN_C90_LIGHT_INDICATOR_COCKPIT);
      PORT_C90_LIGHT_RI_F |= (1 << PIN_C90_LIGHT_RI_F);
      PORT_C90_LIGHT_RI_B |= (1 << PIN_C90_LIGHT_RI_B);
      PORT_C90_LIGHT_LI_F |= (1 << PIN_C90_LIGHT_LI_F);
      PORT_C90_LIGHT_LI_B |= (1 << PIN_C90_LIGHT_LI_B);
      g_music_duration = 0;
      g_current_music = (uint16_t*)pgm_read_word(&g_music[song_idx-1]);
      g_selected_music = (uint16_t*)pgm_read_word(&g_music[song_idx-1]);
      FLAG_MUSIC = 1;
      g_current_alarm_settle_time = g_settings.alarm_settle_time;
      g_alarm_snapshot[0] = 0;
      g_alarm_snapshot[1] = 0;
      g_alarm_snapshot[2] = 0;
    }
    // save the AVERAGE accelerometer values as the alarm trigger reference during the settlement
    if (g_alarm_snapshot[0]) {
      g_alarm_snapshot[0] = ((g_alarm_snapshot[0] + g_adc_voltage[1])/2);
    } else {
      g_alarm_snapshot[0] = g_adc_voltage[1];
    }
    if (g_alarm_snapshot[1]) {
      g_alarm_snapshot[1] = ((g_alarm_snapshot[1] + g_adc_voltage[2])/2);
    } else {
      g_alarm_snapshot[1] = g_adc_voltage[2];
    }
    if (g_alarm_snapshot[2]) {
      g_alarm_snapshot[2] = ((g_alarm_snapshot[2] + g_adc_voltage[3])/2);
    } else {
      g_alarm_snapshot[2] = g_adc_voltage[3];
    }
    // alarm settle time is over: only start alarm with valid accelerometer voltages
    if ((!g_current_alarm_settle_time) && ((g_alarm_snapshot[0] > g_settings.alarm_thres_min) && (g_alarm_snapshot[0] < g_settings.alarm_thres_max)) &&
       ((g_alarm_snapshot[1] > g_settings.alarm_thres_min) && (g_alarm_snapshot[1] < g_settings.alarm_thres_max)) &&
       ((g_alarm_snapshot[2] > g_settings.alarm_thres_min) && (g_alarm_snapshot[2] < g_settings.alarm_thres_max))) {
      // prepare for alarm mode
      FLAG_ALARM_SETTLE = 0;
      all_lights_off();
      g_alarm_counter = g_settings.alarm_counter;
      g_trigger_counter = 0;
      g_state = ST_ALARM;
    }
  }
}

// triggers alarm if movement (voltage change) is high enough 
// 1.5g setting:  Sensitivity: 800 mV/g  -1g = 850mV  0g = 1650mV 1g = 2450mV
// 1 degree tilt is about 9mv, so by default: if the voltage differs 90mv (~10 degrees), for a certain period, the alarm will trigger
void check_alarm_trigger() {
  if (g_state == ST_ALARM) {
    if (FLAG_ALARM_TRIGGER) {
      if (FLAG_ALARM_BLINK) {
        FLAG_ALARM_BLINK = 0;
        PORT_C90_LIGHT_RI_F ^= (1 << PIN_C90_LIGHT_RI_F);
        PORT_C90_LIGHT_RI_B ^= (1 << PIN_C90_LIGHT_RI_B);
        PORT_C90_LIGHT_LI_F ^= (1 << PIN_C90_LIGHT_LI_F);
        PORT_C90_LIGHT_LI_B ^= (1 << PIN_C90_LIGHT_LI_B);
        PORT_C90_LIGHT_INDICATOR_COCKPIT ^= (1 << PIN_C90_LIGHT_INDICATOR_COCKPIT);
        PORT_C90_CLAXON ^= (1 << PIN_C90_CLAXON);
        g_alarm_counter--;
        if (!g_alarm_counter) {
          all_lights_off();
          FLAG_ALARM_TRIGGER = 0; // reset alarm trigger
          g_state = ST_ALARM_SETTLE; // go back to new alarm settle mode
          FLAG_ALARM_SETTLE = 0; // reset alarm settle
        }
      }
    } else if (FLAG_ALARM_BLINK) {
      FLAG_ALARM_BLINK = 0;
      if (g_alarm_blink_counter % 4 == 0) { // blink for 1 tick every timer1 4 counts
        PORT_C90_LIGHT_INDICATOR_COCKPIT |= (1 << PIN_C90_LIGHT_INDICATOR_COCKPIT);
      } else {
        PORT_C90_LIGHT_INDICATOR_COCKPIT &= ~(1 << PIN_C90_LIGHT_INDICATOR_COCKPIT);
      }
      if ((abs(g_adc_voltage[1] - g_alarm_snapshot[0]) > g_settings.alarm_trigger) ||
       (abs(g_adc_voltage[2] - g_alarm_snapshot[1]) > g_settings.alarm_trigger) || 
       (abs(g_adc_voltage[3] - g_alarm_snapshot[2]) > g_settings.alarm_trigger)) {
        g_trigger_counter++;
        if (g_trigger_counter >= g_settings.alarm_trigger_counter) {
          FLAG_ALARM_TRIGGER = 1;
        }
      }
    }
  }
}

uint8_t get_event() {
  uint8_t ev;
  if (g_buffer_tail != g_buffer_head) { // not empty
    ev = g_event_buffer[g_buffer_tail];
    g_buffer_tail++;
    if (g_buffer_tail >= C90_EVENT_BUFFER_SIZE) {
      g_buffer_tail = 0;
    }
    return ev;
  } else {
    return EV_VOID; // just keep returning a void event
  }
}

void set_event(uint8_t ev) {
  g_event_buffer[g_buffer_head] = ev; // insert event at head position
  g_buffer_head++; // advance head
  if (g_buffer_head >= C90_EVENT_BUFFER_SIZE) {
    g_buffer_head = 0; // cycle back to start
  }
  if (g_buffer_head == g_buffer_tail) {
    g_buffer_tail++; // also move tail, basically destroying an event to make space
  }
  if (g_buffer_tail >= C90_EVENT_BUFFER_SIZE) {
    g_buffer_tail = 0; // cycle back to start
  }
}

void process_ri_off() {
  if (FLAG_DEBOUNCE_RI) { // check for 3 positives based on 5ms timer
    g_ri_debounce = (g_ri_debounce << 1);
    FLAG_DEBOUNCE_RI = 0; // reset to wait for next timer event
    if (((g_ri_debounce & 0b00000111) << 5) == 0) {
      remove_substate(ST_RI); // debouncing done, remove state
      // disable indicators
      PORT_C90_LIGHT_RI_F &= ~(1 << PIN_C90_LIGHT_RI_F); // front
      PORT_C90_LIGHT_RI_B &= ~(1 << PIN_C90_LIGHT_RI_B); // rear
      if (g_settings.indicator_sound) {
        PORT_C90_BUZZER &= ~(1 << PIN_C90_BUZZER);
      }
      PORT_C90_LIGHT_INDICATOR_COCKPIT &= ~(1 << PIN_C90_LIGHT_INDICATOR_COCKPIT); // cockpit
    }
  }
}

void process_ri_on() {
  if (FLAG_DEBOUNCE_RI) { // check for 3 positives based on 5ms timer
    g_ri_debounce = (g_ri_debounce << 1) | 0x01;
    FLAG_DEBOUNCE_RI = 0; // reset to wait for next timer event
    if (((g_ri_debounce & 0b00000111) == 0b00000111) && (FLAG_BLINK_RI)) { // blink indicators
      PORT_C90_LIGHT_RI_F ^= (1 << PIN_C90_LIGHT_RI_F);
      PORT_C90_LIGHT_RI_B ^= (1 << PIN_C90_LIGHT_RI_B);
      PORT_C90_LIGHT_INDICATOR_COCKPIT ^= (1 << PIN_C90_LIGHT_INDICATOR_COCKPIT);
      if (g_settings.indicator_sound) {
        PORT_C90_BUZZER ^= (1 << PIN_C90_BUZZER);
      }
      FLAG_BLINK_RI = 0; // reset to wait for next timer event
      if (!get_substate(ST_RI)) { // first time to blink
        TCNT1 = 0; // set 0.5 sec timer counter explicitly to 0, so the first blink happens exactly 0.5 secs later
        set_substate(ST_RI);
      }
    }
  }
}

void process_li_off() {
  if (FLAG_DEBOUNCE_LI) { // check for 3 positives based on 5ms timer
    g_li_debounce = (g_li_debounce << 1);
    FLAG_DEBOUNCE_LI = 0; // reset to wait for next timer event
    if (((g_li_debounce & 0b00000111) << 5) == 0) {
      remove_substate(ST_LI); // debouncing done, remove state
      // disable indicators
      PORT_C90_LIGHT_LI_F &= ~(1 << PIN_C90_LIGHT_LI_F); // front
      PORT_C90_LIGHT_LI_B &= ~(1 << PIN_C90_LIGHT_LI_B); // rear
      if (g_settings.indicator_sound) {
        PORT_C90_BUZZER &= ~(1 << PIN_C90_BUZZER);
      }
      PORT_C90_LIGHT_INDICATOR_COCKPIT &= ~(1 << PIN_C90_LIGHT_INDICATOR_COCKPIT); // cockpit
    }
  }
}
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
int main(void) {
  initialize();
  while(1) {
    command_process();
    dispatch_events();
    while ((g_event = get_event()) != EV_VOID) { // handle the complete event queue in one go
      for (uint8_t i=0; i<TR_CNT; i++) {
        //TODO: swap if-statements
        if (g_trans[i].check_func()) { // check if state matches
          if (g_event == g_trans[i].event) { // check if event matches
            g_trans[i].process_func(); // call event handler
            break;
          }
        }
      }
    }
    if (!g_mcu_reset) { 
      wdt_reset(); // reset the watchdog, i.e. don't reset the mcu
    }
  }
  return 0;
}

// EOF

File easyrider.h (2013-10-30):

/*
 *
 *  Copyright (C) 2013 Bas Brugman
 *  http://www.visionnaire.nl
 *
 *  Licensed under the Apache License, Version 2.0 (the "License");
 *  you may not use this file except in compliance with the License.
 *  You may obtain a copy of the License at
 *
 *    http://www.apache.org/licenses/LICENSE-2.0
 *
 *  Unless required by applicable law or agreed to in writing, software
 *  distributed under the License is distributed on an "AS IS" BASIS,
 *  WITHOUT WARRANTIES OR CONDITIONS OF ANY KIND, either express or implied.
 *  See the License for the specific language governing permissions and
 *  limitations under the License.
 *
 */
#ifndef _EASYRIDER_H_INCLUDED
#define _EASYRIDER_H_INCLUDED

#include <stdint.h>
#include <avr/io.h>
#include <avr/pgmspace.h>

#include "settings.h"

#define STATUS_C90_SENSE_LIGHT_RI                   PINA & (1 << PIN_C90_SENSE_LIGHT_RI) 
#define STATUS_C90_SENSE_LIGHT_LI                   PINA & (1 << PIN_C90_SENSE_LIGHT_LI) 
#define STATUS_C90_SENSE_PILOT                      PINA & (1 << PIN_C90_SENSE_PILOT) 
#define STATUS_C90_SENSE_LIGHT                      PINA & (1 << PIN_C90_SENSE_LIGHT) 
#define STATUS_C90_SENSE_BRAKE                      PINB & (1 << PIN_C90_SENSE_BRAKE) 
#define STATUS_C90_SENSE_ALARM                      PINB & (1 << PIN_C90_SENSE_ALARM) 
#define STATUS_C90_SENSE_IGN                        PINB & (1 << PIN_C90_SENSE_IGN) 
#define STATUS_C90_SENSE_CLAXON                     PINB & (1 << PIN_C90_SENSE_CLAXON) 
#define STATUS_C90_SENSE_WARNING                    PIND & (1 << PIN_C90_SENSE_WARNING) 
#define STATUS_C90_SENSE_RESERVE                    PIND & (1 << PIN_C90_SENSE_RESERVE) 

#define PIN_C90_SENSE_LIGHT_RI                      PINA4 
#define PIN_C90_SENSE_LIGHT_LI                      PINA5 
#define PIN_C90_SENSE_PILOT                         PINA6 
#define PIN_C90_SENSE_LIGHT                         PINA7 
#define PIN_C90_SENSE_BRAKE                         PINB0 
#define PIN_C90_SENSE_ALARM                         PINB1 
#define PIN_C90_SENSE_IGN                           PINB2 
#define PIN_C90_SENSE_CLAXON                        PINB3 
#define PIN_C90_SENSE_WARNING                       PIND0
#define PIN_C90_SENSE_RESERVE                       PIND1

#define PORT_C90_SENSE_LIGHT_RI                     PINA 
#define PORT_C90_SENSE_LIGHT_LI                     PINA 
#define PORT_C90_SENSE_PILOT                        PINA 
#define PORT_C90_SENSE_LIGHT                        PINA 
#define PORT_C90_SENSE_BRAKE                        PINB 
#define PORT_C90_SENSE_ALARM                        PINB 
#define PORT_C90_SENSE_IGN                          PINB 
#define PORT_C90_SENSE_CLAXON                       PINB 
#define PORT_C90_SENSE_WARNING                      PIND 
#define PORT_C90_SENSE_RESERVE                      PIND 

#define DDR_C90_SENSE_LIGHT_RI                      DDRA 
#define DDR_C90_SENSE_LIGHT_LI                      DDRA 
#define DDR_C90_SENSE_CLAXON                        DDRB
#define DDR_C90_SENSE_BRAKE                         DDRB
#define DDR_C90_SENSE_PILOT                         DDRA
#define DDR_C90_SENSE_LIGHT                         DDRA
#define DDR_C90_SENSE_ALARM                         DDRB
#define DDR_C90_SENSE_IGN                           DDRB
#define DDR_C90_SENSE_WARNING                       DDRD 
#define DDR_C90_SENSE_RESERVE                       DDRD 

#define DDR_C90_LIGHT_RI_F                          DDRC 
#define DDR_C90_LIGHT_RI_B                          DDRC 
#define DDR_C90_LIGHT_LI_F                          DDRC 
#define DDR_C90_LIGHT_LI_B                          DDRC 
#define DDR_C90_LIGHT_INDICATOR_COCKPIT             DDRC 
#define DDR_C90_LIGHT_STATUS_COCKPIT                DDRC 
#define DDR_C90_CLAXON                              DDRD
#define DDR_C90_BRAKE                               DDRC
#define DDR_C90_PILOT                               DDRD
#define DDR_C90_LIGHT                               DDRC
#define DDR_C90_BUZZER                              DDRD
#define DDR_C90_HEARTBEAT_LED                       DDRD

#define PORT_C90_LIGHT_RI_F                         PORTC
#define PORT_C90_LIGHT_LI_F                         PORTC
#define PORT_C90_LIGHT_RI_B                         PORTC
#define PORT_C90_LIGHT_LI_B                         PORTC
#define PORT_C90_LIGHT_INDICATOR_COCKPIT            PORTC
#define PORT_C90_LIGHT_STATUS_COCKPIT               PORTC
#define PORT_C90_CLAXON                             PORTD
#define PORT_C90_BRAKE                              PORTC
#define PORT_C90_PILOT                              PORTD
#define PORT_C90_LIGHT                              PORTC
#define PORT_C90_BUZZER                             PORTD
#define PORT_C90_HEARTBEAT_LED                      PORTD

#define PIN_C90_LIGHT_RI_F                          PINC0
#define PIN_C90_LIGHT_LI_F                          PINC1
#define PIN_C90_LIGHT_RI_B                          PINC3
#define PIN_C90_LIGHT_LI_B                          PINC4
#define PIN_C90_LIGHT_INDICATOR_COCKPIT             PINC2
#define PIN_C90_LIGHT_STATUS_COCKPIT                PINC5
#define PIN_C90_CLAXON                              PIND6
#define PIN_C90_BRAKE                               PINC7
#define PIN_C90_PILOT                               PIND7
#define PIN_C90_LIGHT                               PINC6
#define PIN_C90_BUZZER                              PIND5
#define PIN_C90_HEARTBEAT_LED                       PIND4

#define PIN_C90_ADC_BATTERY                         PINA0
#define PIN_C90_ADC_ACCEL_X                         PINA1
#define PIN_C90_ADC_ACCEL_Y                         PINA2
#define PIN_C90_ADC_ACCEL_Z                         PINA3

#define EV_VOID                                  0 
#define EV_ANY                                   1
#define EV_RI_ON                                 2
#define EV_LI_ON                                 3
#define EV_RI_OFF                                4
#define EV_LI_OFF                                5
#define EV_CLAXON_ON                             6
#define EV_CLAXON_OFF                            7
#define EV_BRAKE_ON                              8
#define EV_BRAKE_OFF                             9
#define EV_PILOT_ON                             10 
#define EV_PILOT_OFF                            11
#define EV_LIGHT_ON                             12
#define EV_LIGHT_OFF                            13
#define EV_ALARM_ON                             14 
#define EV_ALARM_OFF                            15 
#define EV_READ_BATT                            16
#define EV_READ_ACCEL                           17
#define EV_IGN_ON                               18
#define EV_IGN_OFF                              19
#define EV_WARNING_ON                           20
#define EV_WARNING_OFF                          21
#define EV_BACKPEDAL                            22
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

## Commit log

2013-03-24 Change alarm trigger time and fixed buzzer sound when turning ignition off
    [command_handlers.c, easyrider.c, easyrider.h]
2013-03-29 Fixed a bug which caused the claxon sound to continue, even when the alarm was turned off
    [easyrider.c]
2013-10-30 Extracted REV B Board and Software to its own repository, REV A will contain only bug fixes from now on
    [easyrider.h]
